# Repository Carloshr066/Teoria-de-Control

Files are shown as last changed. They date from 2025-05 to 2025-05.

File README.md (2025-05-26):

# Teoria-de-Control

Repositorio de github para el proyecto del pendulo invertido de la asignatura de Teoria de control. Tambien incluye las librerias de los PIDs de las prácticas de tiempo discreto.

## Estructura de archivos
- Pendulo_inv.ino: Codigo principal del pendulo invertido.
- Calibrate_sensor.ino: Codigo para calibrar el sensor del pendulo invertido.
- Archivos_diseño_pendulo: Carpeta que contiene los archivos de diseño del pendulo, tanto la PCB y esquema electrico como el modelo 3d del chasis.
- Librerias_PIDs: Carpeta que contiene los archivos de las librerias que implementan los distintos tipos de PIDs de tiempo discreto.

## Metodología seguida
- Selección de los componentes eléctricos y mecánicos para el proyecto
 
- Diseño del esquema electrico y PCB, seguiendo el esquema de conexiones de los componentes.

- Diseño del chasis en base a los componentes elegidos y la PCB diseñada.
 
- Montaje y prueba de los componentes en la PCB fabricada.
 
- Implementación del codigo inicial en la ESP32.
 
- Ajuste del codigo para su correcto funcionamiento.

## Componentes:

  - Esp32 devkit:
    Como parte central del pendulo se ha usado una Esp32 devkit para controlar el pendulo.
    
  - ROB-14450:
    Puente H capaz de controlar 2 motores DC a la vez, permite un voltaje de alimentación de hasta 15v.
    
  - SEN0142:
    Sensor con giroscopio y acelerometro incorporado, usado para medir el angulo del robot y corregirlo.
    
  - LM7805CT/NOPB:
    Transistor para regular el voltaje, tiene un voltaje de salida de 5V perfecto para alimentar la Esp32 devkit y permite hasta 35V de entrada.
    
  - Conectores XT30:
    Se han usado tres pares de conectores XT30 para conectar tanto la batería como los motores la placa.
    
  - Motores DC:
    Para mover el robot se han usado dos motores DC con un tren de engranajes reductor para incrementar el torque.
    
  - Ruedas:
    Se han usado un par de ruedas compatibles con el eje de los motores.
    
  - Batería:
    Se ha usado una batería recargable de 6V para todo el robot.
## Chasis:
El chasis se ha diseñado con la intención de tener un centro de gravedad alineado con el eje de los motores para maximizar la establidad del robot. El chasis en si es muy sencillo, una superficie plana con 4 agujeros para atornillar la placa al chasis y 2 ranuras en los laterales para poner los motores.

## Montaje:
El montaje de robot del robot ha sido principalmente soldar los componentes en la PCB, una vez esta esta lista se han usado unos separadores para que la placa quede separada una cierta distancia del chasis, espacio en el que se ha puesto la batería para tener un perfil más bajo. Con la placa y la batería puestas solo falta colocar los motores en cada estremo del chasis y ponerles las ruedas.

## Ajuste del PID:
La constante Kp del PID se ha ido subiendo en pequeños incrementos hasta que se el robot ha sido capaz de levantarse por su cuenta. Debido a la estabilidad de base del robot poco más ha sido necesario. La constante Ki se ha incrementado hasta que el robot erá capaz de eliminar el pequeño error residual al encontrarse casi perpendicular a la superficie. La constante Kd se incremento muy ligeramente para aumentar la velocidad de respuesta del robot.

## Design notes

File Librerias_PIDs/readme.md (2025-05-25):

# PIDs discretos para Arduino

Librerías que implementan distintos tipos de PIDs en tiempo discreto.

## Tipos de PID

- PID estandar
- PID con filtro IIR
- PID con filtro pasa baja

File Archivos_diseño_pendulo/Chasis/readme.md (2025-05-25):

# Archivos de diseño del chasis

Archivos del diseño 3d del chasis para el pendulo invertido incluye:

- Archivo .FCStd para FreeCad
- Archivos .stl y .obj para el slicer de elección
- Archivo .gcode ya laminado para la impresión

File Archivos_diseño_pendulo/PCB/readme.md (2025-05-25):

# Archivos de diseño de la PCB
Incluye:
- El archivo del esquema eléctrico
- El archivo del diseño de la pcb
- Los ficheros gerber y de taladrado

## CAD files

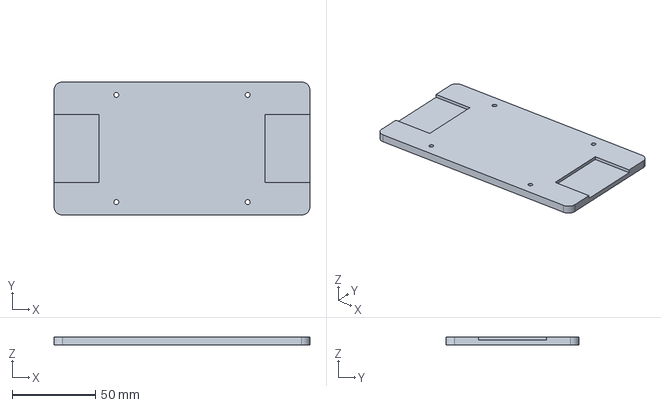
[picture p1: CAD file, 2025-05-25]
Archivos_diseño_pendulo/Chasis/Pendulo_invertido_chasis.FCStd
154.0 x 80.0 x 5.00 mm

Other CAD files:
Archivos_diseño_pendulo/Chasis/Pendulo_invertido_chasis.obj
Archivos_diseño_pendulo/Chasis/Pendulo_invertido_chasis.stl

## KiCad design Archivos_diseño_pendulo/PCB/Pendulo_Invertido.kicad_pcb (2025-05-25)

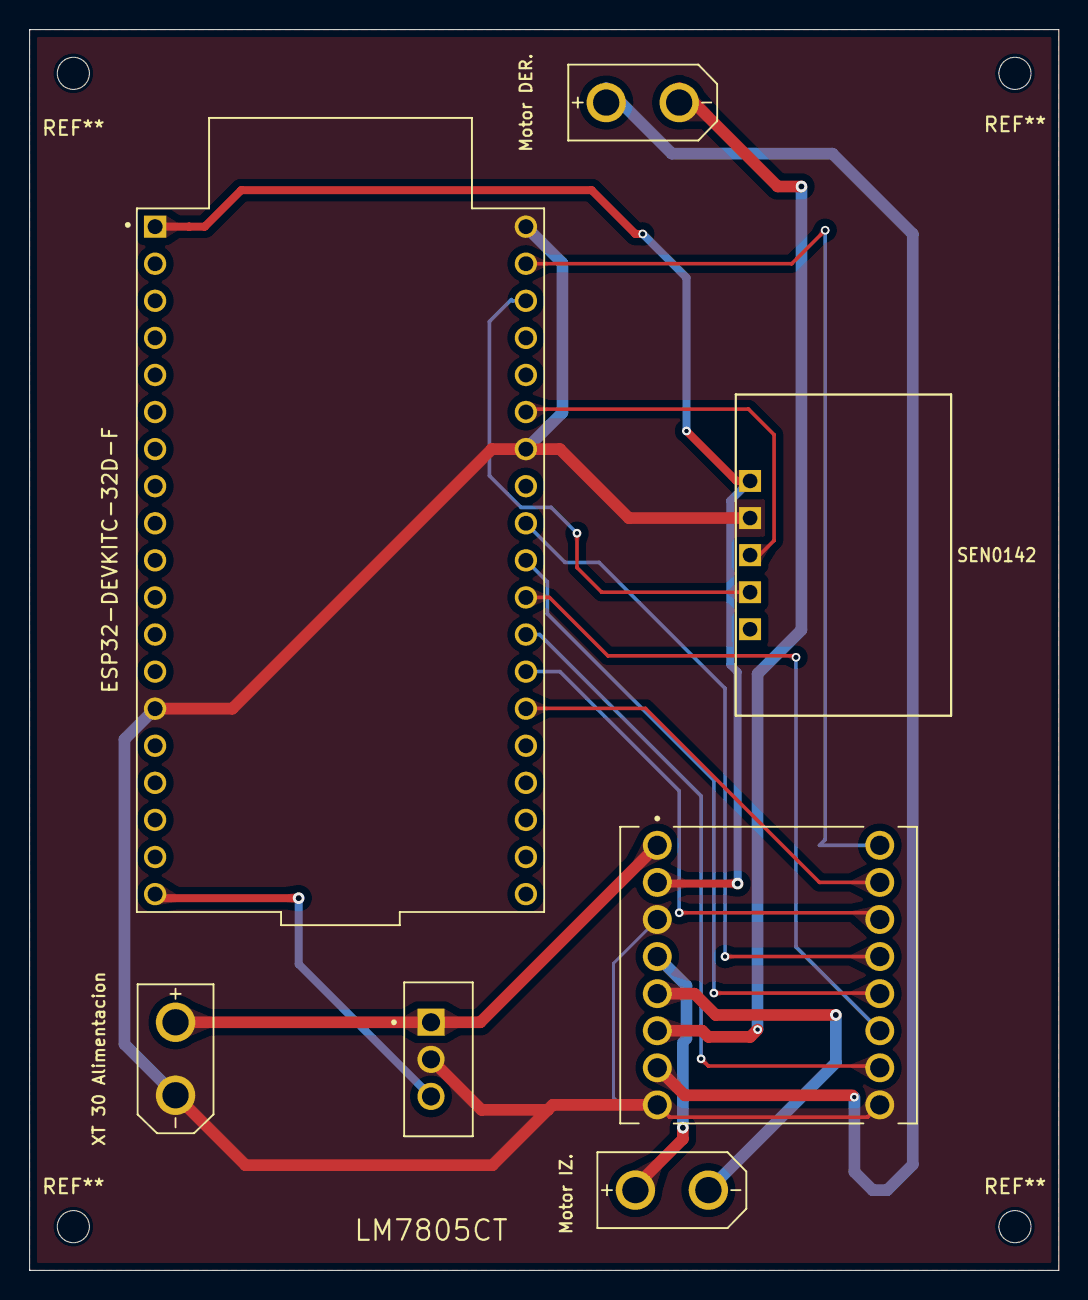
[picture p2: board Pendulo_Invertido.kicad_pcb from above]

Board: 2 copper layers, 70.5 x 85.0 mm, 7 parts (0 on the bottom side), 17 nets.

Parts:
ESP32-DEVKITC-32D-F: ESP32-DEVKITC; MODULE_ESP32-DEVKITC
LM7805CT: LM7805CT_NOPB; TO254P1054X470X1955-3
Motor DER.: XT30UPB-M
Motor IZ.: XT30UPB-M
ROB-1445: ROB-14450; MODULE_ROB-14450
SEN0142: SEN0142
XT 30 Alimentacion: XT30UPB-M

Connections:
+3.3V: ESP32-DEVKITC-32D-F.1 (3V3), ROB-1445.2 (VCC), SEN0142.1 (VIN)
+5V: ESP32-DEVKITC-32D-F.19 (EXT_5V), LM7805CT.3 (OUT)
+6V: LM7805CT.1 (IN), ROB-1445.1 (VM), XT 30 Alimentacion.P$1 (+)
GND: ESP32-DEVKITC-32D-F.14 (GND1), ESP32-DEVKITC-32D-F.32 (GND2), ESP32-DEVKITC-32D-F.38 (GND3), LM7805CT.2 (GND), ROB-1445.3 (GND), ROB-1445.8 (GND), ROB-1445.9 (GND), SEN0142.2 (GND), XT 30 Alimentacion.P$2 (-)
unnamed: ESP32-DEVKITC-32D-F.36 (IO22), SEN0142.4 (SCL)
unnamed: ESP32-DEVKITC-32D-F.33 (IO21), SEN0142.3 (SDA)
unnamed: ESP32-DEVKITC-32D-F.25 (IO0), ROB-1445.15 (AI2)
unnamed: ESP32-DEVKITC-32D-F.26 (IO4), ROB-1445.14 (AI1)
unnamed: ESP32-DEVKITC-32D-F.29 (IO5), ROB-1445.12 (BI1)
unnamed: ESP32-DEVKITC-32D-F.27 (IO16), ROB-1445.10 (PWMB)
unnamed: ESP32-DEVKITC-32D-F.28 (IO17), ROB-1445.11 (BI2)
unnamed: ESP32-DEVKITC-32D-F.30 (IO18), ROB-1445.13 (STBY)
unnamed: ESP32-DEVKITC-32D-F.37 (IO23), ROB-1445.16 (PWMA)
unnamed: Motor IZ..P$1 (+), ROB-1445.4 (A01)
unnamed: Motor IZ..P$2 (-), ROB-1445.5 (A02)
unnamed: Motor DER..P$1 (+), ROB-1445.7 (B01)
unnamed: Motor DER..P$2 (-), ROB-1445.6 (B02)

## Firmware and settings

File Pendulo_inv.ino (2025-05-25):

#include <Wire.h>
#include <I2Cdev.h>
#include <MPU6050.h>

MPU6050 sensor;

// Definiciones de pines de motores
const int pinPWMA = 23;
const int pinAIN2 = 4;
const int pinAIN1 = 0;
const int pinPWMB = 16;
const int pinBIN1 = 5;
const int pinBIN2 = 17;
const int pinSTBY = 18;

// Variables del sensor MPU6050
int16_t ax, ay, az;
int16_t gx, gy, gz;
long tiempo_prev;
float dt;
float ang_x, ang_y;
float ang_x_prev, ang_y_prev;

// Variables PID
float Kp = 5; // Ajusta estos valores según sea necesario
float Ki = 10;
float Kd = 0.1;
float integral = 0.0;
float derivative = 0.0;
float previous_error = 0.0;

void setup() {
  Serial.begin(115200);
  Wire.begin(21, 22); // Pines SDA = 32, SCL = 33
  delay(500);//Evitar errores en el arranque
  sensor.initialize();
  
  if (!sensor.testConnection()) {
  Serial.println("Error: No se pudo conectar con el MPU6050");
  while (1); // Detiene el programa si no hay conexión
  }


  tiempo_prev = millis();

  // Configurar pines de motores
  pinMode(pinAIN2, OUTPUT);
  pinMode(pinAIN1, OUTPUT);
  pinMode(pinPWMA, OUTPUT);
  pinMode(pinBIN1, OUTPUT);
  pinMode(pinBIN2, OUTPUT);
  pinMode(pinPWMB, OUTPUT);
  pinMode(pinSTBY, OUTPUT);
}

void loop() {
  // Obtener datos del MPU6050
  sensor.getAcceleration(&ax, &ay, &az);
  sensor.getRotation(&gx, &gy, &gz);

  // Calcular ángulos con el acelerómetro
  float accel_ang_x = atan(ay / sqrt(pow(ax, 2) + pow(az, 2))) * (180.0 / PI);
  float accel_ang_y = atan(-ax / sqrt(pow(ay, 2) + pow(az, 2))) * (180.0 / PI);

  // Calcular ángulo de rotación con giroscopio y filtro complementario
  dt = (millis() - tiempo_prev) / 1000.0;
  if (dt <= 0) return;

  tiempo_prev = millis();
  ang_x = 0.98 * (ang_x_prev + (gx / 131.0) * dt) + 0.02 * accel_ang_x;
  ang_y = 0.98 * (ang_y_prev + (gy / 131.0) * dt) + 0.02 * accel_ang_y;

  ang_x_prev = ang_x;
  ang_y_prev = ang_y;

  // Control del péndulo invertido usando PID
  float desired_angle = 0.0;
  float error = desired_angle - ang_x;

  integral += error * dt;
  derivative = (error - previous_error) / dt;

  float motor_speed = Kp * error + Ki * integral + Kd * derivative;
  
  motor_speed = constrain(motor_speed, -200, 200);

  // Verificar si motor_speed es NaN y establecerlo en 0 si lo es
  if (isnan(motor_speed)) {
    motor_speed = 0;
  }


  // Controlar los motores
  enableMotors();
  moveMotor(pinPWMA, pinAIN1, pinAIN2, motor_speed);
  moveMotor(pinPWMB, pinBIN1, pinBIN2, motor_speed);

  // Mostrar los ángulos y la velocidad de los motores
  Serial.print("Rotación en X: ");
  Serial.print(ang_x);
  Serial.print(", Error: ");
  Serial.print(error);
  Serial.print(", Velocidad de los motores: ");
  Serial.println(motor_speed);

  previous_error = error;
  enableMotors();
  delay(1); // Aumentar frecuencia de muestreo
  enableMotors();
}

// Funciones adicionales
void moveMotor(int pinPWM, int pinIN1, int pinIN2, float speed) {
  if (speed > 0) {
    digitalWrite(pinIN1, HIGH);
    digitalWrite(pinIN2, LOW);
    analogWrite(pinPWM, speed);
  } else {
    digitalWrite(pinIN1, LOW);
    digitalWrite(pinIN2, HIGH);
    analogWrite(pinPWM, -speed);
  }
}

void enableMotors() {
  digitalWrite(pinSTBY, HIGH);
}

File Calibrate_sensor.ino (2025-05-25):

#include <Wire.h>
#include <I2Cdev.h>
#include <MPU6050.h>

// Dirección del MPU6050 (0x68 o 0x69 dependiendo del estado de AD0)
MPU6050 sensor;

// Valores RAW del acelerómetro y giroscopio
int16_t ax, ay, az;
int16_t gx, gy, gz;

// Variables para el filtro pasa bajos
long f_ax, f_ay, f_az;
int p_ax, p_ay, p_az;
long f_gx, f_gy, f_gz;
int p_gx, p_gy, p_gz;
int counter = 0;

// Offsets
int ax_o, ay_o, az_o;
int gx_o, gy_o, gz_o;

void setup() {
  Serial.begin(57600);
  Wire.begin(21,22);
  sensor.initialize();

  if (sensor.testConnection()) {
    Serial.println("Sensor iniciado correctamente");
  }

  // Leer offsets actuales
  ax_o = sensor.getXAccelOffset();
  ay_o = sensor.getYAccelOffset();
  az_o = sensor.getZAccelOffset();
  gx_o = sensor.getXGyroOffset();
  gy_o = sensor.getYGyroOffset();
  gz_o = sensor.getZGyroOffset();

  Serial.println("Offsets:");
  Serial.print(ax_o); Serial.print("\t");
  Serial.print(ay_o); Serial.print("\t");
  Serial.print(az_o); Serial.print("\t");
  Serial.print(gx_o); Serial.print("\t");
  Serial.print(gy_o); Serial.print("\t");
  Serial.println(gz_o);
  Serial.println("\n\nEnvíe cualquier caracter para empezar la calibración\n\n");

  while (!Serial.available()) {}
  Serial.println("Calibrando, no mover IMU");
}

void loop() {
  // Leer acelerómetro y giroscopio
  sensor.getAcceleration(&ax, &ay, &az);
  sensor.getRotation(&gx, &gy, &gz);

  // Filtro pasa bajos
  f_ax = f_ax - (f_ax >> 5) + ax;
  p_ax = f_ax >> 5;

  f_ay = f_ay - (f_ay >> 5) + ay;
  p_ay = f_ay >> 5;

  f_az = f_az - (f_az >> 5) + az;
  p_az = f_az >> 5;

  f_gx = f_gx - (f_gx >> 3) + gx;
  p_gx = f_gx >> 3;

  f_gy = f_gy - (f_gy >> 3) + gy;
  p_gy = f_gy >> 3;

  f_gz = f_gz - (f_gz >> 3) + gz;
  p_gz = f_gz >> 3;

  // Cada 100 lecturas, ajustar offset
  if (counter == 100) {
    Serial.print("Promedio:\t");
    Serial.print(p_ax); Serial.print("\t");
    Serial.print(p_ay); Serial.print("\t");
    Serial.print(p_az); Serial.print("\t");
    Serial.print(p_gx); Serial.print("\t");
    Serial.print(p_gy); Serial.print("\t");
    Serial.println(p_gz);

    // Calibrar acelerómetro (1g en Z)
    ax_o += (p_ax > 0) ? -0.1 : 0.1;
    ay_o += (p_ay > 0) ? -0.1 : 0.1;
    az_o += ((p_az - 16384) > 0) ? -0.1 : 0.1;

    sensor.setXAccelOffset(ax_o);
    sensor.setYAccelOffset(ay_o);
    sensor.setZAccelOffset(az_o);

    // Calibrar giroscopio (0 en todos los ejes)
    gx_o += (p_gx > 0) ? -0.1 : 0.1;
    gy_o += (p_gy > 0) ? -0.1 : 0.1;
    gz_o += (p_gz > 0) ? -0.1 : 0.1;

    sensor.setXGyroOffset(gx_o);
    sensor.setYGyroOffset(gy_o);
    sensor.setZGyroOffset(gz_o);

    counter = 0;
  }

  counter++;
}
